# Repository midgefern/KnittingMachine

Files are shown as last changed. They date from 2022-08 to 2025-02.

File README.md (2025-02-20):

# A 3D-printable flatbed knitting machine

## Contents
[Before you start](#before-you-start)

[How to use this code](#how-to-use-this-code)

[How to build the machine](#how-to-build-the-machine)

[Basic use and tips](#basic-use)

[Table of 3D printed parts and slicer settings](#3d-printed-parts-and-slicer-settings)

## Before you start

If you are interested in the background, motivations, research, and design process for this project, and especially if you'd like to contribute, please check out the [video series](https://www.youtube.com/playlist?list=PLWDnfcUpk7PLQRvfuGytMauK_sR6CEwI9).

Please keep in mind that this is a passion project and a work-in-progress, not a finished product. You may find bugs or imperfections and if you do I hope you will report them, kindly and patiently. This machine probably won't do everything you could possibly want a knitting machine to do; I am open to hearing your cool feature ideas but I can't promise if or when I'll implement them. 

**IMPORTANT: knitting machine needles are not all interchangeable**, and this machine has been designed to work with a specific model: when sourcing your needles please look for those intended to work with Brother models KR830 / KR838 / KR850.  

## How to use this code

In this project, you will find several types of file:

1. In the **STL** directory you can find pre-compiled models of parts with the default settings, ready to be sliced for 3D printing. If you're not interested in customizing or tinkering and just want to start printing parts, open this folder and skip to the next section, [How to build the machine](#how-to-build-the-machine).

1. The **SCAD** directory contains the modelling code, which can be viewed and edited in [OpenSCAD](https://openscad.org/). This code is divided into:
    - **parts** files, each of which can render and export a single component (or in some cases, pairs of components which are meant to be printed together);
    - **assemblies**, which help visualize how the components will fit together; and
    - **modules**, utility code and parameters which are shared across multiple parts and assemblies.

        - If you want or need to make changes, the key parameters are in **modules/params.scad**. Values that are open to tweaking are named in ```camelCase```; for example, you may want to change the number of needles in a bed, set a custom spacing between needles, adjust the size of screw holes, or fine-tune the tolerances. (Note that you will also need to open individual parts files to view and export your updated models after saving the changes in **params.scad**.) However, you should avoid changing values marked as constants in ```SCREAMING_SNAKE_CASE```. These are carefully calibrated to the needle dimensions and should generally not be changed without also adjusting the cam design and associated SVG assets to compensate. I DO NOT recommend you make changes to the cam layout unless you are very familiar with the project and committed to doing A LOT of testing.

1. The **SVG** directory contains 2D shape assets exported from the technical drawings, which are imported by the SCAD files and extruded into 3D parts such as cams, etc. You shouldn't need to access or modify these files directly.

1. The **Technical Sketches** directory contains design drawings which can be opened in Adobe Illustrator; these can be used to inspect the cam layout, obtain precise measurements and coordinates, and export SVG assets. These are provided for reference, I DO NOT recommend you make changes to the cam layout unless you are very familiar with the project and committed to doing A LOT of testing.

## How to build the machine

[A video demonstration is also available](https://youtu.be/eFesPhYR8KI).

### Printing and supplies

A table of printable parts along with suggested slicer settings can be found below, based on my own tests slicing in Cura and printing with PLA/PLA Pro filament on an Ender 3 V2; note that times and filament weights given are estimates and your experience may vary depending on your printer and slicer. A list of other required hardware, supplies and tools is also provided below.

The needlebed in the provided STL files holds 25 needles at a standard (4.5mm) gauge; if you want a bed with a different number or spacing of needles, these parameters can be changed in **SCAD/modules/params.scad**; you will then need to export the updated models from **needlebed.scad**, **backCover.scad**, and **spongeBar.scad** in **SCAD/parts/**. Multiple needlebeds can be connected in series to create a wider work area. 

**Please note** that knitting machine needles are not all interchangeable, and this machine has been designed to work with a specific model: when sourcing your needles please look for those intended to work with Brother models KR830 / KR838 / KR850.

I recommend sourcing all your hardware before printing your parts.

### Assembling the needlebeds

You will need to print:

- left and right carriage rests
- 2x carriage rest clamp
- 2x clamp head
- 2x clamp bolt (omit if using metal clamp hardware, see note)
- 2x clamp nut (omit if using metal clamp hardware, see note)
- one or more needlebeds (I recommend starting with one and testing before printing additional bed)
- one back cover per needlebed
- one sponge bar per needlebed

You will also need:

- latch-hook knitting machine needles (KR830 / KR838 / KR850), one per  needlebed slot for each bed
- self-adhesive foam weatherstrip (or similar; for sponge bar), 1/4" - 3/8" wide, enough length to span all connected needlebeds, plus a small trimming allowance
- round head machine screws: 
    * #4-40 x 1/2", 4 per needlebed (for back cover)
    * #4-40 x 3/4", 2 per needlebed (for sponge bar)
    * #6-32 x 1/2", 8 (for carriage rests/clamps)
- screwdriver
- scissors or utility knife (to cut foam weatherstrip)
- NOTE: I have been using a 5/16" x 3.5" metal eyebolt in the clamp; the eye is easy to grab and turn without a tool, but not essential. You will need a longer bolt if you choose the "deep" clamp option. If you choose to generate 3D printed bolts for your clamp with an external library, a bolt with an 8mm OD and 12mm nut (between flats) should fit the other connected parts.

For each needlebed:

1. Insert a needle into each slot with the hook end towards the angled edge of the bed; ensure needles are sliding smoothly (sand any imperfections if necessary).
2. Screw back cover to rear of needlebed with #4-40 x 1/2" screws (in any orientation; it's symmetrical). Ensure screw heads are sunk in the well below the surface of the cover but be careful not to overtighten.
3. Cut and apply foam strip to fit the flat underside of the sponge bar; make a cut through the foam strip at the position of each screw hole for the screw to pass through.
4. Screw sponge bar into place with #4-40 x 3/4" screws, taking care that the foam strip doesn't get caught between the spacer and the cover; once in place, the sponge bar should be flush with the surface of the rest of the needlebed. Once again, ensure the screw heads do not protrude, but avoid overtightening.

For each carriage rest:

1. Remove 3D printing supports, sanding any resulting rough surfaces if needed. 
2. Screw the clamp to the bottom of the carriage rest with #6-32 x 1/2" screws, ensuring that the surfaces are flush.
3. Insert the clamp nut into the hexagonal cutout in the clamp, and the bolt from the opposite side; once the bolt has cleared the nut, insert the tip of the bolt into the clamp head, and (when all beds are connected) tighten to the table. (You may choose to glue or otherwise permanently affix the nut and the clamp head; I keep mine separate since they are a tight fit around my table.)

To connect the carriage rests and beds:
1. Slide the slots on the left-hand edge of the unit over the pegs on the right-hand edge of its neighbour. 
2. Repeat until the desired number of beds have been connected and add the right carriage rest.

### Assembling the MkII carriage

You will need to print:

- back plate
- 2x tension cams, mirrored
- 2x tension pointers
- yarn carrier
- yarn feeder 
- stripper plate (2pc.)
- round head machine screws:
    * 4x #6-32 x 1/2"
    * 6x #4-40 x 1/2"
    * 6x #4-40 x 1/4"
    * 2x #4-40 nuts
    * 2x #4 washers

You will also need:
- pliable jewelry wire, approx. 6-7" (15-18cm)
- sandpaper
- screwdriver
- pliers
- side cutters/nippers (if cutting the wire)
- safety goggles (if cutting the wire)

1. Remove any 3D printing supports and sand any resulting rough surfaces, if needed. 
2. For each tension cam: with the flat side of the back plate down, insert the tension cam's pivot point into the hole; the nut side of the cam will be against the plate in the region of the arc-shaped cutout. Holding the cam in place, flip the assembly over (flat side facing you) and screw the round end of a tension pointer to the underside of the cam pivot, with a #4-40 x 1/4" screw. Insert a washer between the pointer and the plate, and connect the pointer, washer, plate and tension cam with a #4-40 x 1/2" screw.
3. With the angled face of the yarn carrier cover facing down and the cone-shaped side of the yarn feeder facing up, screw the two parts together using #4-40 x 1/4" screws. Flip the yarn carrier assembly over and align the stripper plate pieces under the opposite edge, so that the points of the stripper plate form a small gap under the yarn feeder hole; screw into place with #4-40 x 1/2" screws. 
12. With the flat side of the camplate facing up, align the yarn carrier assembly with the screw holes at the front edge of the camplate (closest to the hold position). Screw into place with #6-32 screws.
13. Create a yarn guide with the jewelry wire by coiling around a small cylinder 3 times; form one end of the coil into a small loop (or otherwise finish the cut edge according to your preference). Form the other end into a flat loop or coil, and wrap around a #6-32 screw; secure the yarn guide with the screw in the middle hole at the back of the carriage, and bend into your preferred position to guide the yarn towards the yarn feeder.

## Basic use

Machine knitting is a skilled craft that takes time and patience to learn. If you've never knit by machine before, be prepared to spend some (maybe a lot of) time practicing techniques. 

A full introduction to machine knitting is beyond the scope of this guide, but there are many approachable lessons elsewhere online; for the most relevant information to this style of machine, I recommend looking for techniques demonstrated on simple, single-bed machines such as the Bond Ultimate Sweater Machine (there are a few differences between those machines and this one but they have a lot of the basics in common). 

Instead, this overview will focus on the peculiarities of this machine and the essentials you'll need to get set up.

### Yarn

This machine uses needles which can knit a range of yarn from ultrafine lace or fingering weights (on the 4.5mm gauge bed) to some lighter worsted weights (on every-other needle or on a 9mm gauge bed), but in my experience the heavier side of that range has behaved unpredictably. Beginners may reduce frustration by looking for smooth, consistent wool or quality acrylic yarns in fingering, sport, or DK weight (best on a 6.5mm bed) for their first projects; avoid bulky or heavily textured "art" yarns, slippery fibers, or very inelastic cotton yarns, at least until you are comfortable with the machine. Yarns must be wound into a ball/cake which feeds smoothly from the centre.

### Weight

Weight must be applied to the knitting as it is created in order to maintain the proper tension and help pull the old stitches over the new ones. I use a weighted hem/cast-on rag with a built-in pocket or channel to hold a metal rod or bar, but you could also use a cast-on rag with claw weights if you already have them. For my weighted hem, I use a flat (rather than tubular) version of the cast-on bonnet with split rings in this [Dean & Bean tutorial](https://www.deanandbean.com/setup-bonnet-pattern-20), but there are many other options to get started: the key features are pre-existing loops to hang onto your needles, and something to attach your weight to so that it is distributed evenly across the width of your project. Experiment with different amounts of weight (you might need more than you expect!) and keep in mind that different projects might require different amounts of weight, too.

Problems that might occur due to insufficient weight include: dropped stitches, unintentional tucked stitches, split stitches.

### Casting on

Push the desired number of needles into a working position (tips of hooks at or just past the edge of the bed). Hang a loop from your cast-on rag/hem onto (at least) every other needle, then add your weights. 

Set the carriage onto the carriage rest, aligning the needlebed's rails with the corresponding channels in the underside of the carriage; the stripper plate will hook under the angled front edge of the needledbed. 

Before knitting with your project yarn, establish several rows of "waste" yarn (this can be reused many times, so it doesn't really need to go to waste). Set the yarn into the carriage by feeding it through the wire coil, over the top of the carriage, and into the slot in the yarn feeder's funnel. Pass the yarn through the gap in the stripper plate and lay it over the stripper plate, away from the direction of knitting. Pull some slack in the yarn out of the ball so that it will feed freely when the carriage is moved.

Ensure the latches of all the working needles are open so that they can receive yarn as the carriage passes over them. Using gentle downward pressure, slide the carriage towards the needles, starting slowly to watch that the first needle catches the yarn; you may need to hold the loose end of the yarn to add a little bit of tension as these first few stitches form. Continue sliding the carriage across the needlebed until all working needles have been cleared. 

Check that new stitches have been formed successfully through every loop and that every needle now holds yarn. If not, you can correct the missed stitches manually (for a few misses) or remove the knitting and rehang the cast-on rag and start again again (for a lot). If stitches are consistently not forming correctly, double-check that: 
- all latches are open
- enough weight has been added
- yarn is feeding through the wire coil guide and into the feeder.

Between rows, pull more yarn out of the ball if necessary so that it will feed freely. Gently tension the yarn with one hand as you slide the carriage back towards the first needle, removing any excessive slack from the yarn feeder so that the loop formed around the first needle is snug, then drop the yarn and let it feed freely once the first couple of stitches have formed.

Once you have established a few rows of waste yarn and stitches are consistently knitting correctly, you can switch to project yarn and cast on using whatever technique is called for in your pattern. For ease of removal later, I recommend separating the waste yarn from the project yarn with a single row of "ravel cord": a thin, smooth, contrasting colour yarn which will easily slide out when pulled, allowing the adjoining pieces to pull apart without cutting the waste yarn.

### Carriage settings and needle positions

Tension can be adjusted by loosening the screws at the sharp end of the tension pointers and pivoting the tension cams to a new position; re-tighten the screws to set the new tension. Pointers set more towards the top edge of the carriage will loosen the tension, while settings towards the side edge of the carriage will tighten the tension. 

Needles with butts aligned all the way to the back of the bed are **out of work**; these needles will not be actuated by any cams in any setting, will not form stitches, and should not hold any yarn. Latches should be closed before placing needles in this position.

The "home" position for needles exiting the carriage is the standard **working position**. Between the working position and the hold position is the **forward working position**, at the point where latches have just pushed forward past the old loop on the needle. With the MkII carriage, needles in both these positions will always knit. The forward working position can be used when returning needles to work from the hold position or other manipulations that leave the live stitch behind the latch. If the stitches are behind the latches in this position, it is important to ensure latches are open before knitting the next row, otherwise the hook will not be able to catch a new loop of yarn before the old loop is dropped.

Needles with their butts aligned all the way to the front of their slots are in **hold position**. These needles will not be actuated and will not knit but can hold live stitches, which is useful for tuck stitches and short rows. Because the stitches are behind the latches in this position, it is particularly important to ensure latches are open before returning the needles to work, or the hook will not be able to catch a new loop of yarn before the old loop is dropped.

### Troubleshooting

As mentioned above, common causes of issues include insufficient weight, improperly closed latches, or yarn not having been properly fed into the yarn guide and yarn feeder; these can cause dropped stitches, skipped/tucked stitches, or split stitches.

Other issues may include:

#### Tension problems

Generally poor tension that can't be fixed within the available range of the tension cams or by changing to a different gauge of needlebed could be a problem if the yarn you have chosen is inappropriate, for example, too thick or too textured for one stitch to pull smoothly through another. Previously good tension can be suddenly affected if the yarn is not flowing freely out of the ball, if it catches on another object, if it gets knotted, or if it gets wrapped around the yarn coil; to correct these problems, pause and check for impediments before re-knitting any problem stitches if necessary.

#### Carriage jams

Sometimes the carriage may jam due to one of its edges catching on part of the needlebed, usually where a connection between two beds is not completely flush; in this case, the jam can usually be cleared by gently lifting the leading edge of the carriage 1-2mm and gently sliding forward. Check that your work surface is flat and smooth, that there are no unexpected objects under any part of the bed, and that your beds haven't warped or deformed.

In some cases the cause of a jam is a needle which has hit an unexpected obstacle due to being out of position: for example, if a needle which should be out of work has slipped forward slightly. Needles can also jam due to tension problems, knots in the yarn, or malformed stitches, which can all prevent needles from actuating through their full range.

Sometimes these needle jams may occur while the needle is underneath the carriage, in which case it is difficult to see the source of the problem. If you can't see or reach the needle to diagnose the problem, I recommend removing the carriage: lift the carriage off the rails, tilt forward to clear the needles, and set aside. Unknit any worked stitches from the unsuccessful pass and reset to start the row again.

Regardless of the cause of the jam, it is important to stop moving the carriage. DO NOT try to push through sudden, unexpected resistance. Sometimes a needle jam can be cleared by *gently* wiggling the carriage back and forth by a centimetre or two, but attempting to force it may damage your machine.

#### Maintenance and storage conditions

Some plastics used for 3D printing are more vulnerable to heat than others. When not in use, store your knitting machine components in dry conditions, at room temperature, and out of direct sunlight. Do not leave the parts in a hot car or near other sources of heat.

Parts which contact the needles, especially the cams, may benefit from a wax or plastic-friendly lubricant in between projects.

When storing the needlebeds, be cautious of the needle hooks and latches; they can be damaged if they get caught on foreign objects or otherwise treated roughly.

## 3D printed parts and slicer settings

|Part |#  |Mirroring  |Orientation |Layer height |Supports? |Infill|Z-seam alignment|Initial layer horizontal expansion  |Print time (est.)|Weight (est., g)|Metres (est.)|
|---|---|---|---|---|---|---|---|---|---|---|---|
|backPlate |1  |n/a |Flat top aligned to plate|.2mm / adaptive layers|None |20% |Sharpest corner |-0.1mm to -0.2mm |12h33 |119 |39.93 |
|tCam |2  |Mirror one |Hex nut up |.2mm |Normal, touching buildplate|100%  |Sharpest corner |-0.1mm to -0.2mm |TBC |TBC |TBC |
|stripperPlate |1  |None |Lay flat |.2mm / adaptive layers|None |100%  |Sharpest corner |-0.1mm to -0.2mm |5h42 |35 |11.84 |
|Yarn feeder |1  |n/a |Lay flat |.12mm / adaptive |None |20% |Default |-0.1mm to -0.2mm |4h02 |25 |8.49 |
|Yarn carrier cover|1  |n/a |Lay flat |.2mm |Below overhang |20% |Default |-0.1mm to -0.2mm |6h57 | | |
|Needlebed |1  |n/a |Lay flat |.2mm |None |15% |Sharpest corner |-0.1mm to -0.2mm |14h12 |111 |37.35 |
|Back cover * |1  |n/a |Lay flat |.2mm |None |20% |Sharpest corner |-0.1mm to -0.2mm |2h53 |23 |7.57 |
|Sponge cover * |1  |n/a |Lay flat |.2mm |None |20% |Sharpest corner |-0.1mm to -0.2mm |see backCover |see backCover |see backCover|
|Carriage rest L |1  |n/a |TBC |TBC |TBC |TBC |TBC |TBC |TBC |TBC |TBC |
|Carriage rest R |1  |n/a |TBC |TBC |TBC |TBC |TBC |TBC |TBC |TBC |TBC |
|Clamps |2  |TBC |TBC |TBC |TBC |TBC |TBC |TBC |TBC |TBC |TBC |
|Clamp heads |2  |TBC |TBC |TBC |TBC |TBC |TBC |TBC |TBC |TBC |TBC |

\* Back cover and sponge bar were sliced and printed in the same job; a combined time/weight estimate is provided

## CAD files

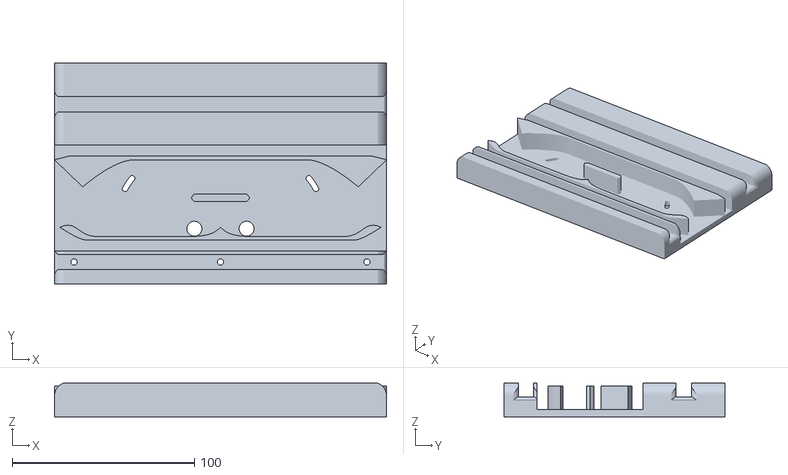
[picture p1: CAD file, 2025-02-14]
STL/backPlate_mk2.stl
182.0 x 121.0 x 18.5

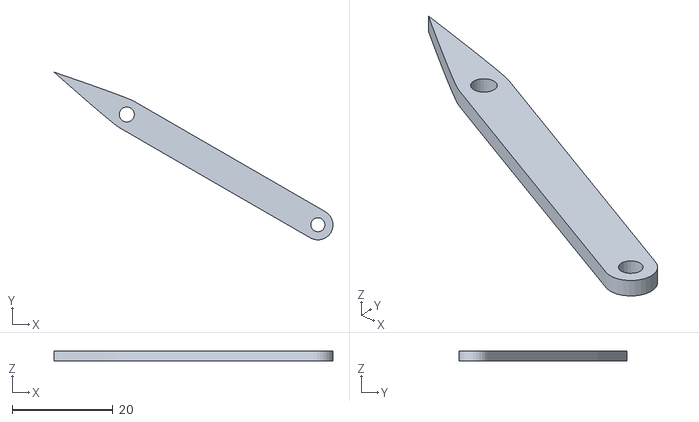
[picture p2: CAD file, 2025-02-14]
STL/tPointer.stl
55.5 x 33.4 x 2.00

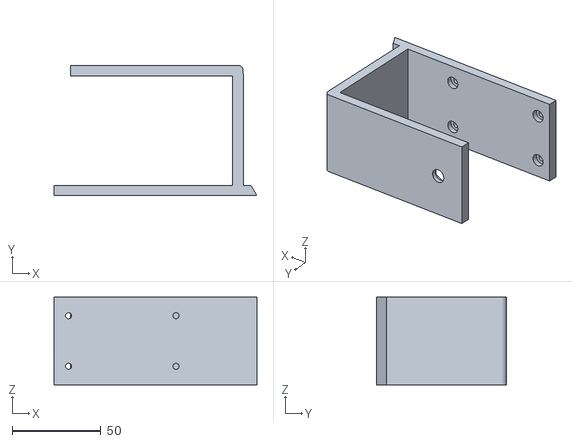
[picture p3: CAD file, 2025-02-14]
STL/clamp.stl
114.7 x 73.7 x 49.6

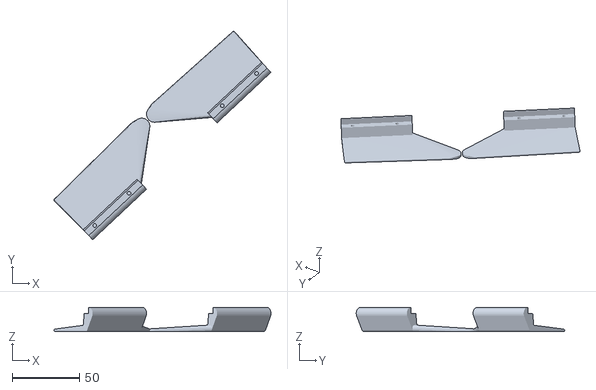
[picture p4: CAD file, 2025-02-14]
STL/stripperPlate.stl
161.4 x 155.2 x 18.2

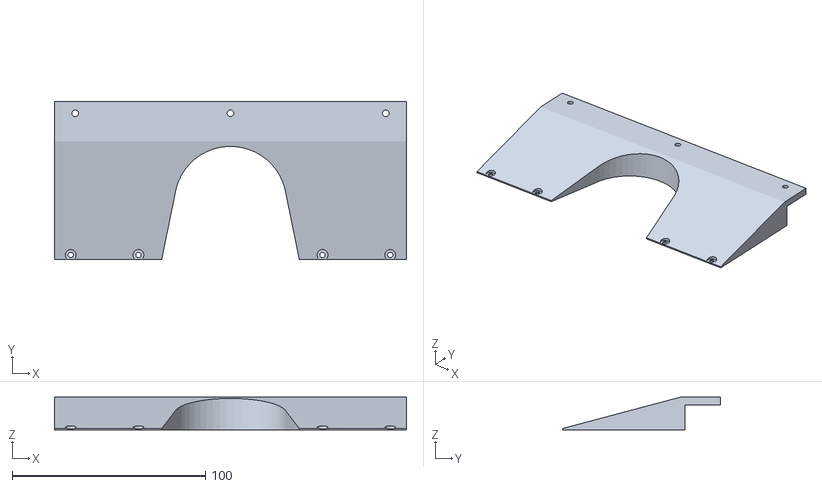
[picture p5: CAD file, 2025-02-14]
STL/yarnCarrierCover.stl
182.0 x 81.5 x 17.0

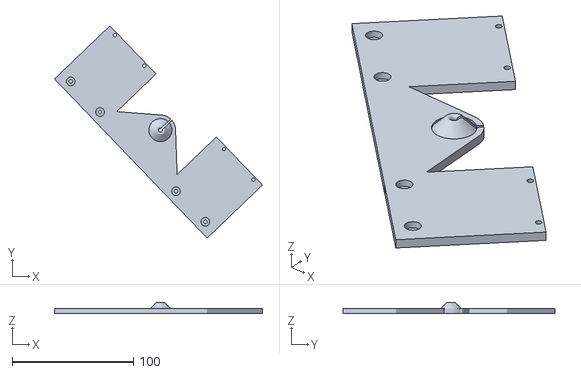
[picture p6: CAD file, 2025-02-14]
STL/yarnFeeder.stl
171.7 x 175.2 x 9.00

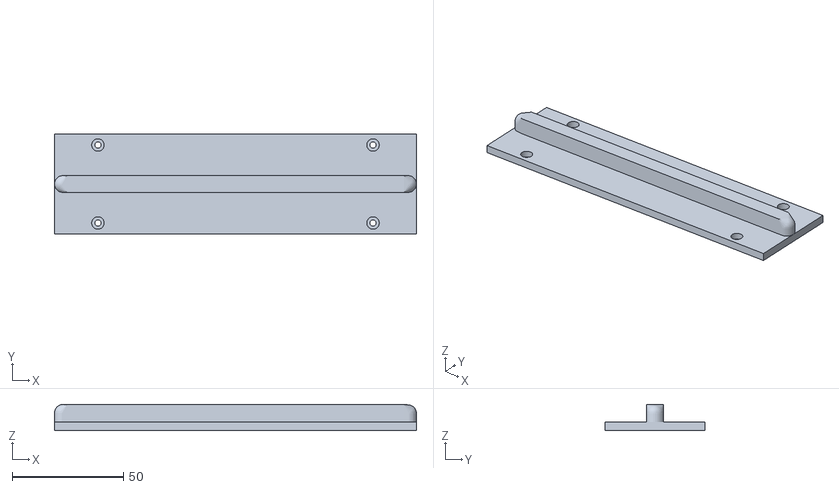
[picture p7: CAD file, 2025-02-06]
STL/backCover_mid.stl
162.5 x 44.8 x 11.7

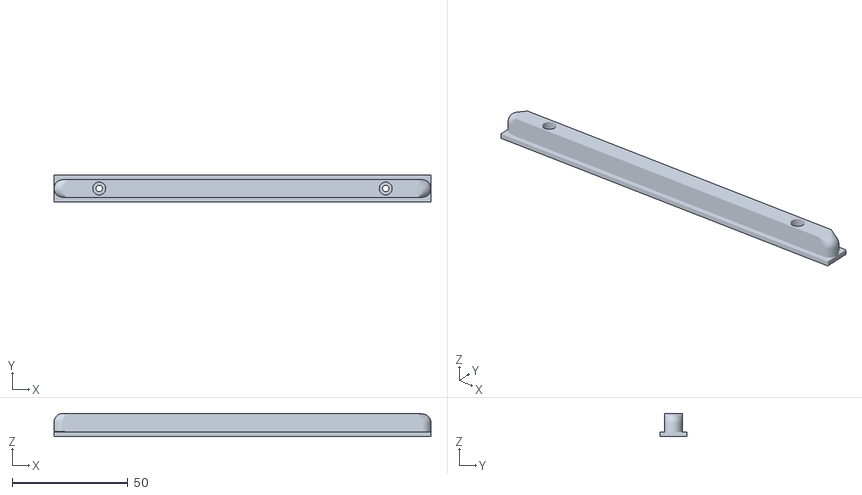
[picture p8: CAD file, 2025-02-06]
STL/spongeBar_mid.stl
162.5 x 11.6 x 10.0

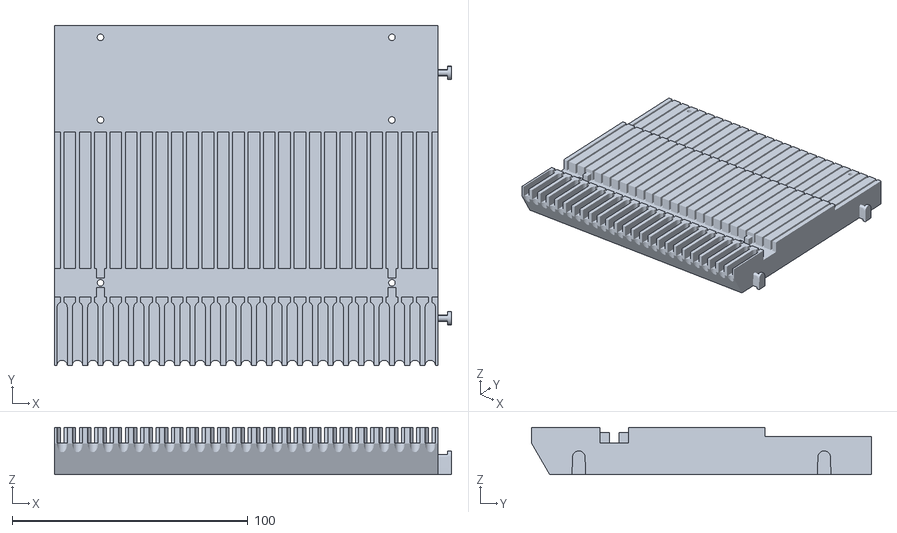
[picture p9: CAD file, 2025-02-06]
STL/needlebed_mid.stl
168.2 x 144.0 x 20.0

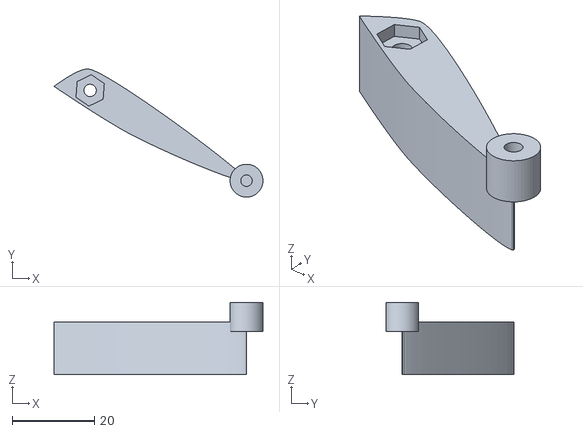
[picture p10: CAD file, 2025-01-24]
STL/tCam_mk2.stl
50.8 x 31.2 x 17.5

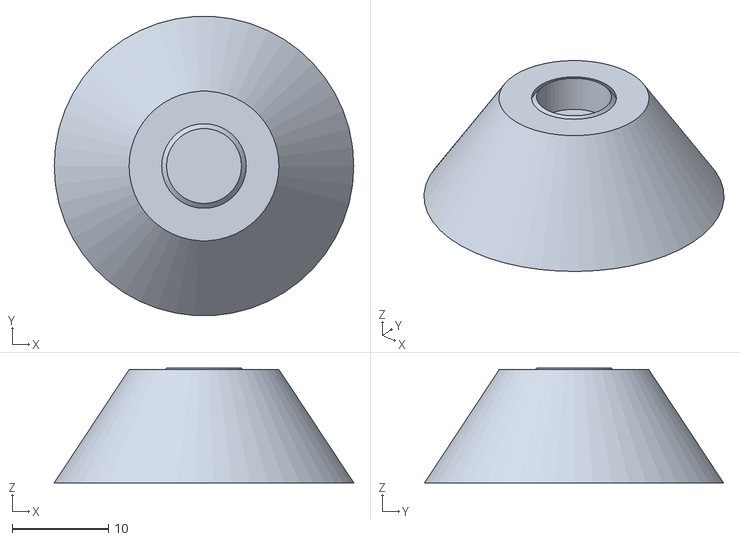
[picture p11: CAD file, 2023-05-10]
STL/clampHead.stl
31.2 x 31.1 x 11.9

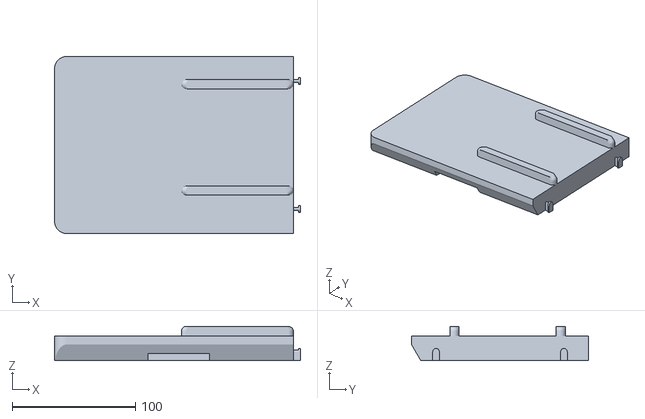
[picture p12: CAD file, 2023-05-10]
STL/carriageRest_L.stl
200.0 x 144.0 x 28.0

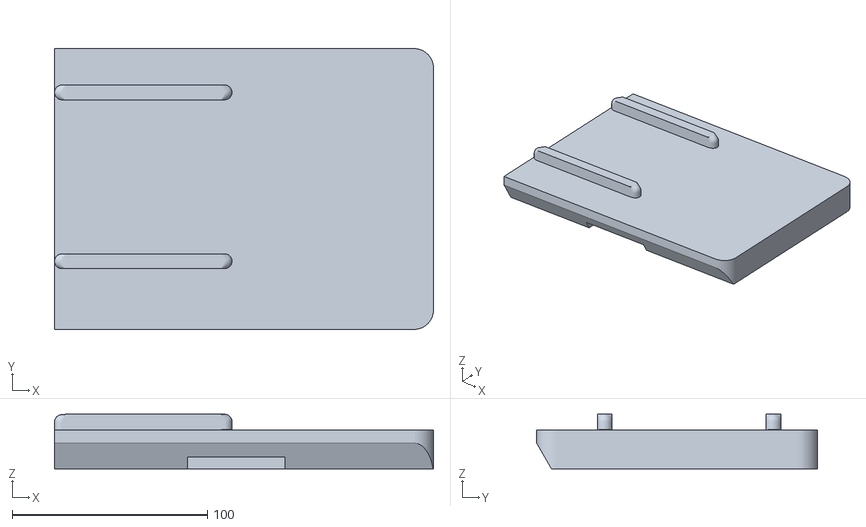
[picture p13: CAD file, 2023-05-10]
STL/carriageRest_R.stl
194.2 x 144.0 x 28.0

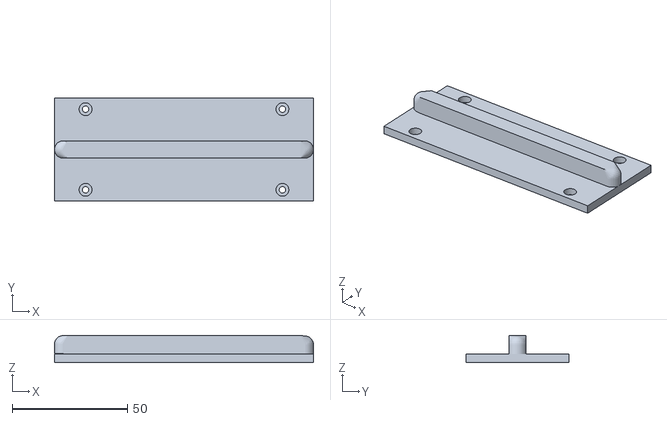
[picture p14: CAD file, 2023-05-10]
STL/backCover_std.stl
112.5 x 44.8 x 11.7

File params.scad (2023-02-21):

/*

Values in `camelCase` are user-variable (within reason); 
values like numNeedles and screwDiam, etc.,  can be modified to
accommodate user preference or hardware subsitution. 

Values in `ALL_CAPS` should be considered CONSTANTS and should
only be modified with *extreme caution* as they will affect the 
relationship between the needles and the cams, which could
prevent stitches from forming correctly.

I recommend only modifying these constants if you are also 
making changes to the cam design in the technical sketch.
*/

gauge = 6.5;
numNeedles = 5;
tolerance = 0.2; // allows a bit of room for parts that have to fit together; adjust according to your printer's precision

// ---
// Hardware dimensions 
// (actual measurements, no tolerances)

// - pan head 6-32 machine screws
screwDiam = 3.45;
screwHeight = 18;
screwHeadDiam = 6.75 + tolerance * 2; 
screwHeadHeight = 2.55 + tolerance * 2;
nutWidth = 7.9;
nutHeight = 2.8;

// - pan head 4-40 machine screws
screwDiamSm = 2.79;
screwHeightSm = 14.62;
screwHeadHeightSm = 2.41 + tolerance * 2;
screwHeadDiamSm = 5.21 + tolerance * 2;

// TODO: look for metric hardware alternatives while abroad 

// ---
// Needle dimensions
// - Brother needles
BUTT_HEIGHT = 15;
NEEDLE_WIDTH = 1.25;
NEEDLE_LEG_HEIGHT = 1.85;
HOOK_DIAM = 3.5;

// ---
// Needle Bed Zones
BACK_COVER = 45;
OOW_TRACK = 8;
B_TRACK = 42; // will divvy up working tracks (B & C position) later
C_TRACK = 0;
WORKING_TRACK = B_TRACK + C_TRACK;
HOLD_TRACK = 8;
SPONGE_BAR = 12;
COMB = 29;
NEEDLE_EXTENSION = 34.5;

// ---
// Needle bed dimensions
NEEDLE_BED_DEPTH = BACK_COVER + OOW_TRACK + WORKING_TRACK + HOLD_TRACK + SPONGE_BAR + COMB;
needleBedHeight = screwHeight + 2;
needleSlotHeight = NEEDLE_LEG_HEIGHT * 2 + screwHeadHeight;
needleSlotWidth = NEEDLE_WIDTH + 0.25; // add a small amount of clearance
combWidth = gauge*2/3; // width of cutouts for stitch formation; this gives room for the thickness of the yarn looped around the needle when it pulls back into the slot, but has to balance leaving enough material for the remaining "teeth" to not be too fragile
spongeThickness = 2.5;
spongeBarThickness = needleSlotHeight - NEEDLE_LEG_HEIGHT - spongeThickness;
YARN_DEPOSIT_Y = -155.1;
YARN_DEPOSIT_Z = -needleSlotHeight + HOOK_DIAM;
connectorOffset = 20;

screwPlacement = 3; // how many needles from edge of bed; min 2, max floor(numNeedles/2)

// ---
// Carriage dimensions
// refer to technical sketch
camHeight = BUTT_HEIGHT; // thickness of the tracks the needles ride along
camPlateHeight = 4; // plate behind the cams
CAM_PLATE_WIDTH = 91 * 2; 
CAM_PLATE_DEPTH = NEEDLE_BED_DEPTH - COMB + 6;

railDepth = 8;
railHeight = 8; // ???
xOffset = 16.5;
//vCamScrews = [[34-xOffset, -90.25, 0],[58-xOffset, -74.25, 0],[86-xOffset,-90.25, 0]];

echo(needleSlotHeight);

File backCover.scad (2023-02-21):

include<params.scad>;
use<needlebedScrews.scad>;
use<roundedRail.scad>;

module backCover(width = gauge) { 

            translate([0,-BACK_COVER/2, -((screwHeadHeight + 1) - tolerance)/2])
            cube([width, BACK_COVER - tolerance, (screwHeadHeight + 1) - tolerance], center = true);
}

module backRail(width = gauge, rounded = false, tolerance = tolerance) {
    translate([0,-BACK_COVER/2, railHeight/2]) {
        if (rounded) {
            roundedRail(width, railDepth - tolerance*2, railHeight);
        } else {
            cube([width, railDepth - tolerance*2, railHeight], center = true);
        }
    }
}

difference() {
    translate([gauge*numNeedles/2 - gauge/2, 0, 0])
    
    backCover(width = numNeedles*gauge);
    needleBedScrews();
}


translate([(gauge*numNeedles)/2 - gauge/2, 0, 0]) 
backRail(width = numNeedles * gauge, rounded = true);        
     

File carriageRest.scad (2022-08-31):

include<params.scad>;
use<needleBed.scad>;
use<backCover.scad>;
use<spongeBar.scad>;
use<connector.scad>;

clampWidth = 50;
clampDepth = NEEDLE_BED_DEPTH-clampWidth/2; 
clampThickness = 6;
clampHollow = 62;

module carriageRest() {
    union() {
        difference() {
            hull() {
                needleBase();   
                translate([-CAM_PLATE_WIDTH, -10, -needleBedHeight/2])
                cylinder(needleBedHeight, 10, 10, center = true); 
                
                translate([-CAM_PLATE_WIDTH, -NEEDLE_BED_DEPTH+10, -needleBedHeight/2])
                cylinder(needleBedHeight, 10, 10, center = true); 
            }
            for(i = [0:ceil(CAM_PLATE_WIDTH/gauge)]) {
               translate([-gauge*i, 0, 0])
               frontAngle(CAM_PLATE_WIDTH + 10);
            }
            // cutout for clamp
            translate([-CAM_PLATE_WIDTH/2, -NEEDLE_BED_DEPTH, -needleBedHeight])
                cube([clampWidth, clampDepth*2, clampThickness*2], center = true); 
            clampScrews();
        }
        translate([gauge/2-CAM_PLATE_WIDTH/4,0,0]) {
            frontRail(CAM_PLATE_WIDTH/2, rounded = true);
            backRail(CAM_PLATE_WIDTH/2, rounded = true);
        }
    }
}

module clampScrews() {
    // screwholes for clamp
    $fn = 50;
    translate([-CAM_PLATE_WIDTH/2,0,-needleBedHeight]) {
        translate([0,-(NEEDLE_BED_DEPTH-clampWidth),0]) {
            translate([- clampWidth/2 + screwHeadDiam*1.5, 0, 0])
            #cylinder(screwHeight*2, d = screwDiam, center = true); 
            
            translate([ - clampWidth/2 + screwHeadDiam*1.5, 0, 0])
            #cylinder((screwHeadHeight + tolerance)*2, d = screwHeadDiam, center = true); 
            
            translate([ + clampWidth/2 - screwHeadDiam*1.5, 0, 0])
            #cylinder(screwHeight*2, d = screwDiam, center = true); 
            
            translate([ + clampWidth/2 - screwHeadDiam*1.5, 0, 0])
            #cylinder((screwHeadHeight + tolerance)*2, d = screwHeadDiam, center = true); 
        }
        translate([0,-clampWidth*2/3,0]) {
            translate([- clampWidth/2 + screwHeadDiam*1.5, 0, 0])
            #cylinder(screwHeight*2, d = screwDiam, center = true); 
            
            translate([ - clampWidth/2 + screwHeadDiam*1.5, 0, 0])
            #cylinder((screwHeadHeight + tolerance)*2, d = screwHeadDiam, center = true); 
            
            translate([ + clampWidth/2 - screwHeadDiam*1.5, 0, 0])
            #cylinder(screwHeight*2, d = screwDiam, center = true); 
            
            translate([ + clampWidth/2 - screwHeadDiam*1.5, 0, 0])
            #cylinder((screwHeadHeight + tolerance)*2, d = screwHeadDiam, center = true); 
        }
    }
}

module clampUnit() {
    difference() {
        // top
        translate([-CAM_PLATE_WIDTH/2 , -NEEDLE_BED_DEPTH + clampDepth/2, -needleBedHeight + clampThickness/2])
            cube([clampWidth - tolerance*2, clampDepth - tolerance, clampThickness-tolerance], center = true); 
        clampScrews();
        for(i = [0:ceil(CAM_PLATE_WIDTH/gauge)]) {
           translate([-gauge*i, 0, 0])
           frontAngle(CAM_PLATE_WIDTH + 10);
        }
    }
    // front
    hull () {
        translate([-CAM_PLATE_WIDTH/2 , -NEEDLE_BED_DEPTH + clampThickness/2 + 12, -(needleBedHeight - tolerance) - clampHollow/2]) {
                cube([clampWidth - tolerance*2, clampThickness, clampHollow], center = true);
            
            // rounded edge
            translate([0,0,-(clampHollow + clampThickness)/2])
            rotate([0,90,0])
            cylinder(clampWidth - tolerance*2, d = clampThickness, center = true, $fn = 30);
        }  
    }
    difference() {
        // bottom
        translate([-CAM_PLATE_WIDTH/2 , -NEEDLE_BED_DEPTH + clampDepth/2 +  clampThickness/2, -(needleBedHeight - tolerance) - clampHollow - clampThickness/2 ])
        cube([clampWidth - tolerance*2, clampDepth - 25, clampThickness], center = true);
        
        
        translate([-CAM_PLATE_WIDTH/2,-clampWidth*2/3 - 18,-(needleBedHeight - tolerance) - clampHollow - clampThickness/2]) {
            // bolt hole
            cylinder(h = clampThickness*2, d = 8, center = true, $fn = 50);
            
            // nut cutout
            translate([-14.491/2,-12.55/2,clampThickness/2]) // use w/h specs from svg
            linear_extrude(6.75, center = true)
            import("SVG/HexNut.svg");
        }        
    }
}


//translate([-gauge,0,0])
//clampUnit();

union() {
    translate([-gauge, 0, 0])
    carriageRest();
    translate([-gauge/2,-connectorOffset,-needleBedHeight])
    connector(tolerance = tolerance);
    translate([-gauge/2,-(NEEDLE_BED_DEPTH-connectorOffset),-needleBedHeight])
    connector(tolerance = tolerance);
}

//difference() {
//translate([gauge*numNeedles, 0, 0])
//mirror([1,0,0])
//carriageRest();
//translate([gauge*numNeedles - gauge/2 - tolerance,-connectorOffset,-needleBedHeight-tolerance])
//connector();
//translate([gauge*numNeedles - gauge/2 - tolerance,-(NEEDLE_BED_DEPTH-connectorOffset),-needleBedHeight - tolerance])
//connector();
//}

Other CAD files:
STL/needlebed_std.stl
STL/spongeBar_std.stl
SCAD/modules/params.scad
SCAD/assemblies/assembly.scad
SCAD/assemblies/camplate.scad
SCAD/assemblies/carriageAssembly.scad
SCAD/assemblies/needlebedAssembly.scad
SCAD/assemblies/yarnCarrier.scad
SCAD/modules/camplate_coords_mk2.scad
SCAD/modules/carriageScrews.scad
SCAD/modules/connector.scad
SCAD/modules/needlebedScrews.scad
SCAD/modules/roundedRail.scad
SCAD/modules/utils.scad
SCAD/parts/backCover.scad
SCAD/parts/backPlate.scad
SCAD/parts/carriageRest.scad
SCAD/parts/clampHead.scad
SCAD/parts/needlebed.scad
SCAD/parts/spongeBar.scad
SCAD/parts/stripperPlate.scad
SCAD/parts/tCam.scad
SCAD/parts/tPointer.scad
SCAD/parts/yarnCarrierCover.scad
SCAD/parts/yarnFeeder.scad
clampHead.scad
needlebed.scad
spongeBar.scad

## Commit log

2022-08-12 needlebed assembly
    [assembly.scad, backCover.scad, needleCover.scad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]
2022-08-15 improve front angle calculation
    [needlebed.scad, params.scad]
2022-08-15 begin carriage rest
    [backCover.scad, carriageRest.scad, needlebed.scad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]
2022-08-16 connector first draft
    [assembly.scad, carriageRest.scad, connector.scad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]
2022-08-16 begin yarn carrier
    [assembly.scad, backCover.scad, connector.scad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]
2022-08-17 this yarn carrier is a mess but we're saving it for posterity
    [params.scad, yarnCarrier.scad]
2022-08-17 new stripper plate component
    [stripperPlate.scad]
2022-08-17 actually include camplate file
    [camplate.scad]
2022-08-17 basic stripper plate shape
    [stripperPlate.scad]
2022-08-17 add yarn feeder
    [params.scad, yarnFeeder.scad]
2022-08-17 figuring out how to align yarn feeder in a printable assembly
    [stripperPlate.scad, yarnFeeder.scad]
2022-08-19 split yarn carrier housing into pieces for improved printing orientation
    [yarnCarrier.scad]
2022-08-19 match widths of stripper plate and yarn carrier
    [params.scad, stripperPlate.scad, yarnCarrier.scad]
2022-08-19 consolidate yarn carrier assembly into one file to avoid circular dependencies
    [stripperPlate.scad, yarnCarrier.scad, yarnFeeder.scad]
2022-08-19 remove unused code and refactor for readability
    [yarnCarrier.scad]
2022-08-21 yarn carrier plate covers whole bottom of carrier for better printing; screw alignment
    [yarnCarrier.scad]
2022-08-31 full printable assembly for testing V2
    [assembly.scad, camplate.scad, carriageRest.scad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]
2022-08-31 modify yarn feeder and carrier for more visual access to needles
    [yarnCarrier.scad]
2022-08-31 two part stripper plate to allow yarn removal
    [yarnCarrier.scad]
2022-08-31 fix gap in stripper plate
    [yarnCarrier.scad]
2022-09-02 add spacer to needlebed to keep spongebar aligned
    [needlebed.scad]
2022-09-04 round off slot in stripper plate to prevent fabric dragging
    [yarnCarrier.scad]
2022-09-04 round inlets of rails to prevent jamming at section joins
    [camplate.scad]
2022-09-04 add other v cam tension options
    [camplate.scad]
2022-09-09 change inner v-cam path to allow room for screw heads
    [camplate.scad]
2022-09-09 round off remaining contact edge of rail
    [camplate.scad]
2022-09-09 refactor screws, connectors
    [assembly.scad, backCover.scad, needlebed.scad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]
2022-09-20 refactor rails and change end rounding
    [backCover.scad, needlebed.scad, spongeBar.scad]
2022-09-30 track SVGs
2022-09-30 track tech sketch
2022-10-05 camplate and carriage mods for mk2
    [camplate.scad, params.scad, yarnCarrier.scad]
2022-10-13 camplate with spring cams
    [camplate.scad]
2022-10-17 fix needlepath with cam overhaul
    [camplate.scad]
2022-10-17 include coords file
    [camplate_coords.scad]
2022-10-25 fix end rounding of rails
    [assembly.scad, backCover.scad, params.scad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]
2022-10-27 use smaller screws for back plate to avoid needle contact at standard gauge
    [backCover.scad, needlebedScrews.scad]
2022-10-27 create two level spring cam insert, plus code cleanup
    [backCover.scad, camplate.scad, camplate_coords.scad]
2022-10-28 differentiate parts by color
    [camplate.scad]
2022-11-01 alignment marks etc
    [camplate.scad, camplate_coords.scad, params.scad]
2022-11-18 fix tolerance on inserts
    [assembly.scad, camplate.scad, params.scad]
2022-11-18 add lever lock and tension pointer
    [leverLock.scad]
2023-02-21 shift yarn pickup toward centre and modify WP cam for cleaner dropoff
    [camplate.scad, camplate_coords.scad, params.scad]
2023-02-21 refactor tPointer
    [camplate.scad, tPointer.scad]
2023-02-21 refactor springCamInsert and dependencies
    [camPinHoles.scad, camplate.scad, params.scad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]
2023-02-21 refactor cams
    [camplate.scad, holdCam.scad, tCam.scad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]
2023-02-21 refactor lever plates
    [leverPlate.scad]
2023-02-21 refactor backPlate
    [backPlate.scad, camplate.scad, carriageScrews.scad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]
2023-02-21 refactor yarn carrier
    [camplate.scad, stripperPlate.scad, yarnCarrier.scad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]
2023-02-21 comment assembly files
    [backPlate.scad, camplate.scad, carriageAssembly.scad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]
2023-02-27 reorganize directory structure
    [assembly.scad, backCover.scad, backPlate.scad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]
2023-05-04 fix unextrudable cam
    [leverLock.scad, springCamInsert.scad, wpCam.scad]
2023-05-04 rollback cam changes
    [camplate_coords.scad]
2023-05-04 include tech sketches
    [tech_sketch-open_cams.dxf]
2023-05-10 add STLs and update carriageRest / clamp
    [backCover_std.stl, backPlate.stl, carriageRest.scad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]
2023-11-30 uncomment carriage rest
    [carriageRest.scad]
2023-12-01 retrofit improved carriage features to mk2 cam layout
    [backPlate.scad, backPlate_mk2.stl, camplate.scad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]
2024-12-11 clean up unused files
    [backPlate.scad, backPlate.stl, camplate.scad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]
2025-01-24 cleanup unused files
    [camPinHoles.scad, tech_sketch-open_cams.dxf]
2025-02-06 include mid-gauge needlebed STLs3
    [backCover_mid.stl, needlebed_mid.stl, params.scad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]
2025-02-14 fresh exports of carriage parts, JIC
    [backPlate_mk2.stl, clamp.stl, params.scad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]
